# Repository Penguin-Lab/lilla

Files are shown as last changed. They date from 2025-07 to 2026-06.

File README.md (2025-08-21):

# lilla
A Lilla é uma robô quadrúpede desenvolvida para andar de forma autônoma ou para ser controlada pelo celular. Para se locomover, ela possui 4 patas de 3 graus de liberdade cada (3 motores) e uma ESP32 que comanda o conjunto! Ela é a quarta integrante robótica do nosso espaço inteligente!

# Estrutura física
A estrutura física do robô é composta por quatro patas de três eixos cada (três motores). As patas são fixadas a uma estrutura de PLA para deixar o robô firme. As peças são todas projetadas em 3D e foram impressas utilizando PLA, podendo ser encontradas na pasta Pecas_3d deste projeto.

   

## Peças 3D em STL
As peças em 3D desenvolvidas para este projeto foram baseadas no projeto do robô desenvolvido por Andres ([LINK](https://gitlab.com/anflores/pavlov_mini)). Na pasta Pecas_3d, estão listadas essas peças em STL. Para ajudar, segue abaixo uma lista de todas as peças que devem ser impressas e qual o valor da sua maior dimensão (para ajudar na escolha da impressora):
* Corpo
  * 1x [LILLA_AXILA_FRONT_LEFT.STL (81 mm)](https://github.com/Penguin-Lab/lilla/blob/main/Pecas_3d/LILLA_AXILA_FRONT_LEFT.STL)
  * 1x [LILLA_AXILA_FRONT_RIGHT.STL (81 mm)](https://github.com/Penguin-Lab/lilla/blob/main/Pecas_3d/LILLA_AXILA_FRONT_RIGHT.STL)
  * 1x [LILLA_AXILA_BACK_LEFT.STL (81 mm)](https://github.com/Penguin-Lab/lilla/blob/main/Pecas_3d/LILLA_AXILA_BACK_LEFT.STL)
  * 1x [LILLA_AXILA_BACK_RIGHT.STL (81 mm)](https://github.com/Penguin-Lab/lilla/blob/main/Pecas_3d/LILLA_AXILA_BACK_RIGHT.STL)
  * 1x [LILLA_SUPPORT_LEFT_TOP.STL (127 mm)](https://github.com/Penguin-Lab/lilla/blob/main/Pecas_3d/LILLA_SUPPORT_LEFT_TOP.STL)
  * 1x [LILLA_SUPPORT_LEFT_TOP.STL espelhado (127 mm)](https://github.com/Penguin-Lab/lilla/blob/main/Pecas_3d/LILLA_SUPPORT_LEFT_TOP.STL)
  * 2x [LILLA_SUPPORT_FACE_BACK_UP.STL (51 mm)](https://github.com/Penguin-Lab/lilla/blob/main/Pecas_3d/LILLA_SUPPORT_FACE_BACK_UP.STL)
  * 2x [LILLA_SUPPORT_FACE_BACK_DOWN.STL (63 mm)](https://github.com/Penguin-Lab/lilla/blob/main/Pecas_3d/LILLA_SUPPORT_FACE_BACK_DOWN.STL)
  * 2x [LILLA_SUPPORT_FACE_BACK_DOWN.STL (63 mm)](https://github.com/Penguin-Lab/lilla/blob/main/Pecas_3d/LILLA_SUPPORT_FACE_BACK_DOWN.STL)
  * 2x [LILLA_SUPPORT_BOTTOM.STL (99 mm)](https://github.com/Penguin-Lab/lilla/blob/main/Pecas_3d/LILLA_SUPPORT_BOTTOM.STL)
  * 4x [LILLA_SUPPORT_PCI.STL (9 mm)](https://github.com/Penguin-Lab/lilla/blob/main/Pecas_3d/LILLA_SUPPORT_PCI.STL)
* Patas
  * 2x [LILLA_TIBIA_LEFT.STL (128 mm)](https://github.com/Penguin-Lab/lilla/blob/main/Pecas_3d/LILLA_TIBIA_LEFT.STL)
  * 2x [LILLA_TIBIA_LEFT.STL espelhado (128 mm)](https://github.com/Penguin-Lab/lilla/blob/main/Pecas_3d/LILLA_TIBIA_LEFT.STL)
  * 2x [LILLA_FEMUR_LEFT_A_1.STL (134 mm)](https://github.com/Penguin-Lab/lilla/blob/main/Pecas_3d/LILLA_FEMUR_LEFT_A_1.STL)
  * 2x [LILLA_FEMUR_LEFT_A_1.STL espelhado (134 mm)](https://github.com/Penguin-Lab/lilla/blob/main/Pecas_3d/LILLA_FEMUR_LEFT_A_1.STL)
  * 4x [LILLA_FEMUR_LEFT_A_2.STL (8 mm)](https://github.com/Penguin-Lab/lilla/blob/main/Pecas_3d/LILLA_FEMUR_LEFT_A_2.STL)
  * 2x [LILLA_FEMUR_LEFT_B.STL (134 mm)](https://github.com/Penguin-Lab/lilla/blob/main/Pecas_3d/LILLA_FEMUR_LEFT_B.STL)
  * 2x [LILLA_FEMUR_LEFT_B.STL espelhado (134 mm)](https://github.com/Penguin-Lab/lilla/blob/main/Pecas_3d/LILLA_FEMUR_LEFT_B.STL)
  * 2x [LILLA_OMBRO_LEFTFRONT_BACKRIGHT.STL (66 mm)](https://github.com/Penguin-Lab/lilla/blob/main/Pecas_3d/LILLA_OMBRO_LEFTFRONT_BACKRIGHT.STL)
  * 2x [LILLA_OMBRO_LEFTFRONT_BACKRIGHT.STL espelhado (66 mm)](https://github.com/Penguin-Lab/lilla/blob/main/Pecas_3d/LILLA_OMBRO_LEFTFRONT_BACKRIGHT.STL)
  * 8x [LILLA_TIBIA_TUBO.STL (20 mm)](https://github.com/Penguin-Lab/lilla/blob/main/Pecas_3d/LILLA_TIBIA_TUBO.STL)
* Rosto e bumbum
  * 1x [LILLA_FRONT_FRAME.STL (137 mm)](https://github.com/Penguin-Lab/lilla/blob/main/Pecas_3d/LILLA_FRONT_FRAME.STL)
  * 1x [LILLA_FACE.STL (137 mm)](https://github.com/Penguin-Lab/lilla/blob/main/Pecas_3d/LILLA_FACE.STL)
  * 1x [LILLA_BUMBUM.STL (137 mm)](https://github.com/Penguin-Lab/lilla/blob/main/Pecas_3d/LILLA_BUMBUM.STL)

Obs 1: para que as patas girem sem forçar a conexão dos eixos dos motores com as peças, são utilizados dois tipos de rolamentos para cada pata: dois rolamentos [6805-2RS 25x37x7](https://pt.aliexpress.com/item/4000347743665.html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) e um rolamentos [606-2RS 6x17x6](https://www.oliveirarolamentos.com.br/micro-rolamento-rigido-de-esferas-606-2rs-c3-6x17x6mm.html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).
Obs 2: para o comando da tibia, o motor deverá ter em seu eixo uma [polia dentada GT2 de 36 dentes para eixo de servo e correia de 6mm](https://a.aliexpress.com/_mPVv40N), e uma [correia de 6mm com 300mm de comprimento](https://a.aliexpress.com/_mN8S5o1).

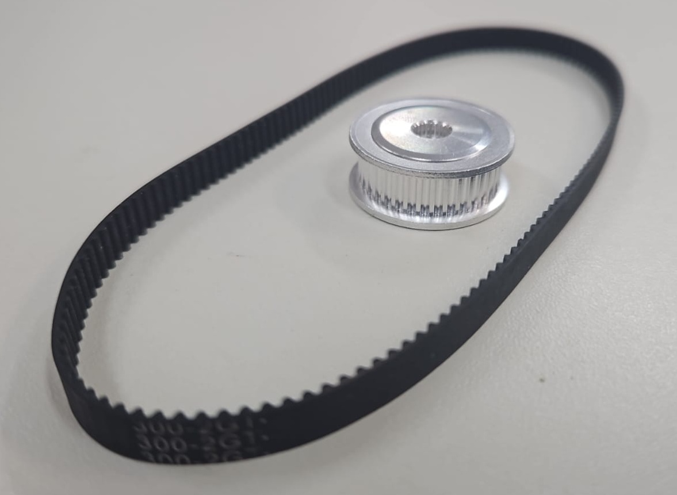
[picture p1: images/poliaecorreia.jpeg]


Obs 3: os outros motores ficam fixados nas peças por [discos metálicos pequenos padrão para eixos de servo](https://a.aliexpress.com/_mPHt3nf).

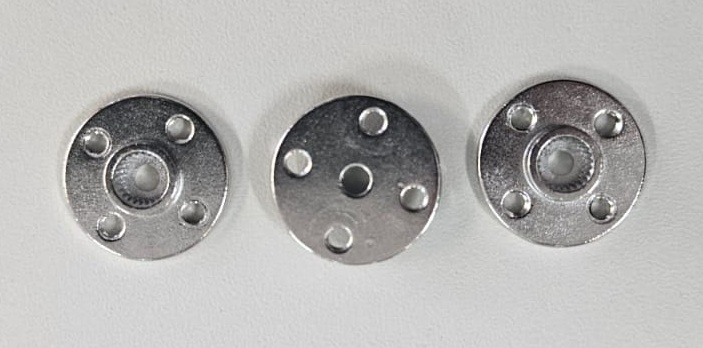
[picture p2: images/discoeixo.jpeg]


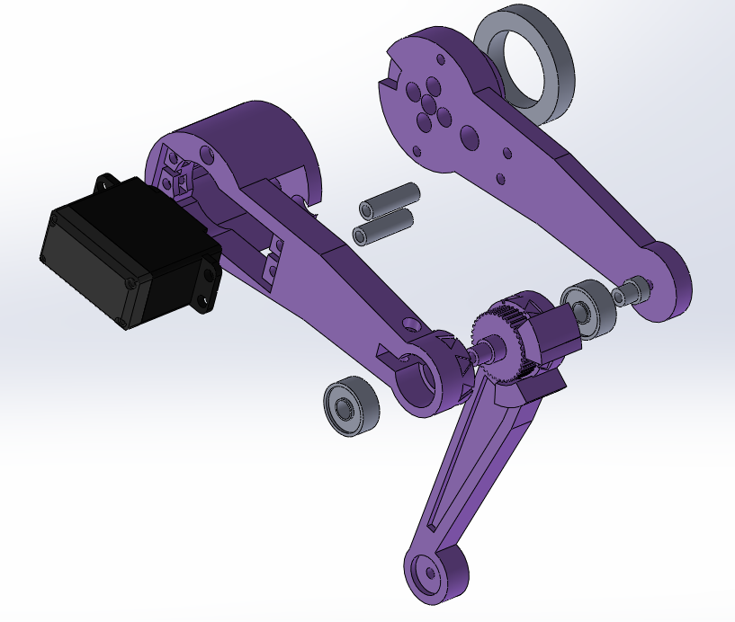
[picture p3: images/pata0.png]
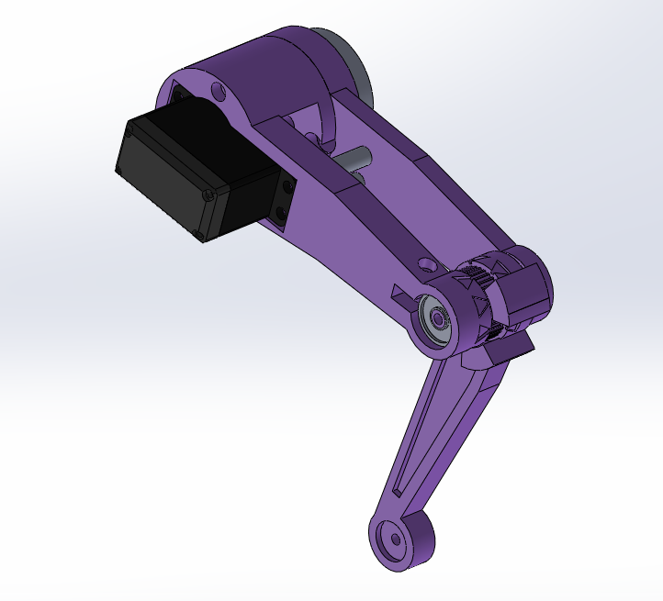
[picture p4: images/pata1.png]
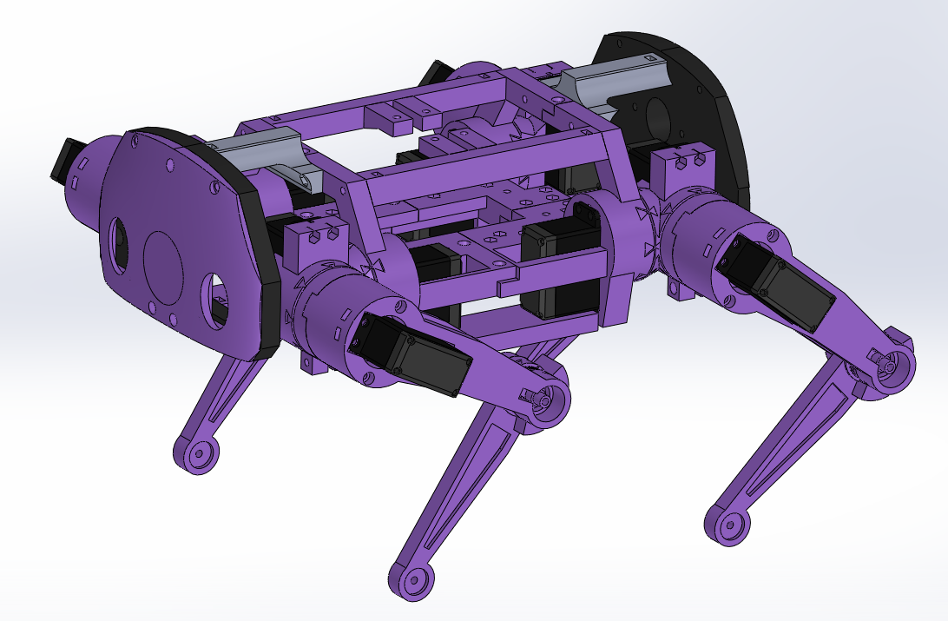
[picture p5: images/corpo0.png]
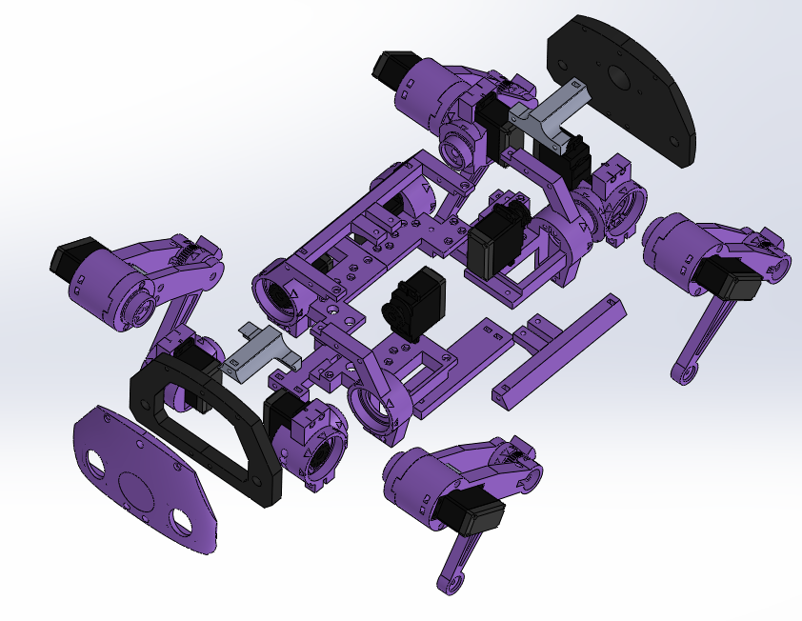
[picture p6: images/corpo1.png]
   

## Outros itens da estrutura
Alguns outros itens são necessários para finalizar a estrutura da Lilla:
* Parafusos m3 de diversos tamanhos
* 4x Tiras de EVA: colocar na ponta das peças de tibia para evitar que o robô deslize no chão

## Placa de circuito impresso
No projeto, foi desenvolvida uma placa de circuito para servir como shield para a ESP32 e conexão com a placa PCA9685 e o módulo DFPlayer Mini MP3 Player.

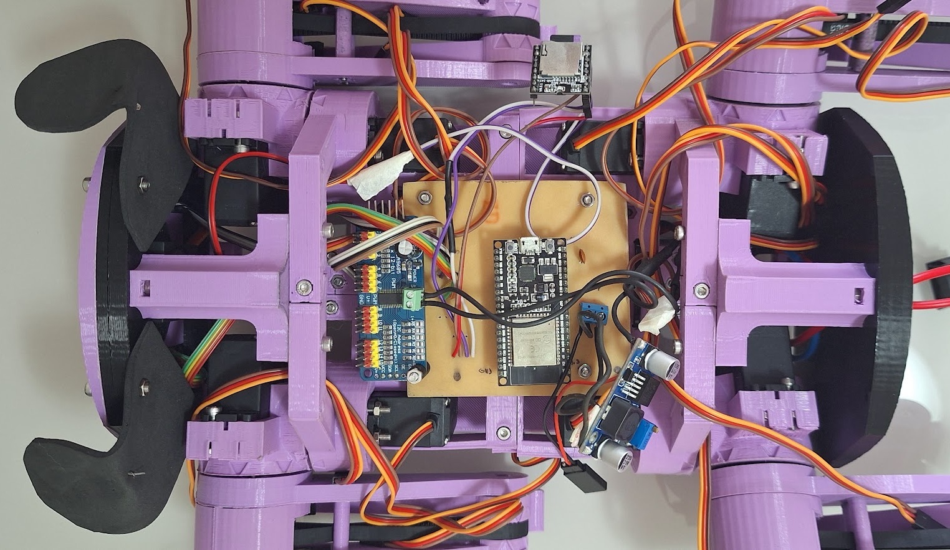
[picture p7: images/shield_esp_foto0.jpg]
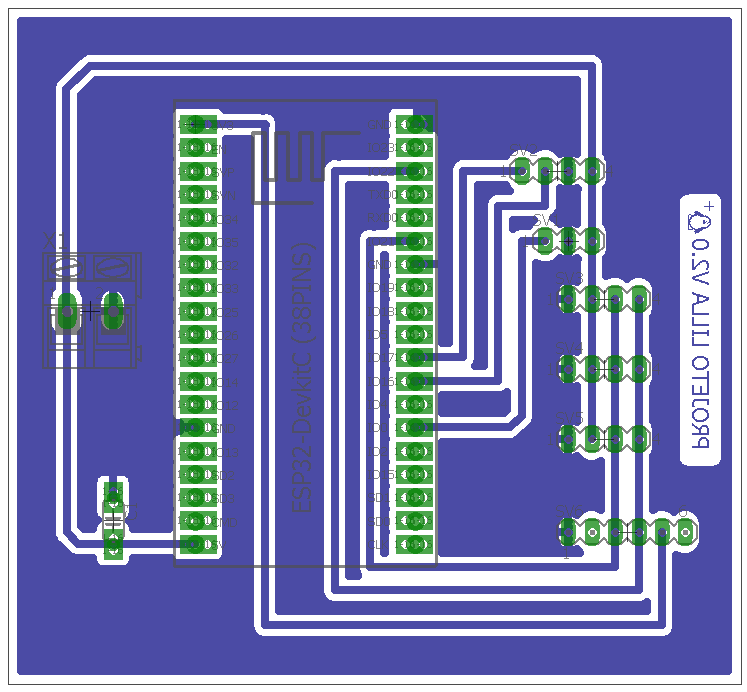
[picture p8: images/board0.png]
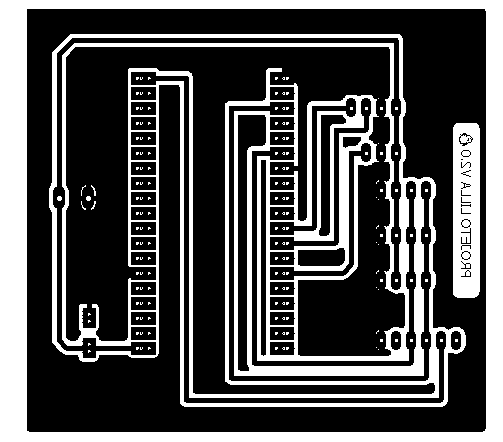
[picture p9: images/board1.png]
  

## Componentes eletrônicos
Os componentes eletrônicos embarcados no robô e equipamentos utilizados são:
* Controlador com Wi-fi e Bluetooth
  * 1x ESP32 (38 pinos)
* Motores
  * 12x Servo TowerPro MG995 Metálico
* 1x Placa PCA9685 para comando dos 12 motores
* 1x Módulo DFPlayer Mini MP3 Player com cartão micro SD contendo aúdio de latidos
* 1x Alto-falante de 3W e 4Ohm para os latidos
* Chave (switch)
* Alimentação
  * Bateria Zippy LiFe 1100mAh 2s 6,6V (ESP32)
  * Bateria TM Hobbies LiFe 2100mAh 2s 6,6v (motores)

# Software
Na pasta de códigos, há um código de programação da ESP32 (38 pinos). Ele é um exemplo em C++ do comando de movimentação da Lilla:
* Dabble: a ESP32 pode se comunicar com o aplicativo Dabble no celular e receber comandos de ação.

## Alunas participantes e desenvolvedoras da Lilla
* Ana Carolina Domingues Benisio
* Jéssica Kauany Morais Carvalho
* Maria Cecilia poton Cristovão
* Sarah Souza Mendes

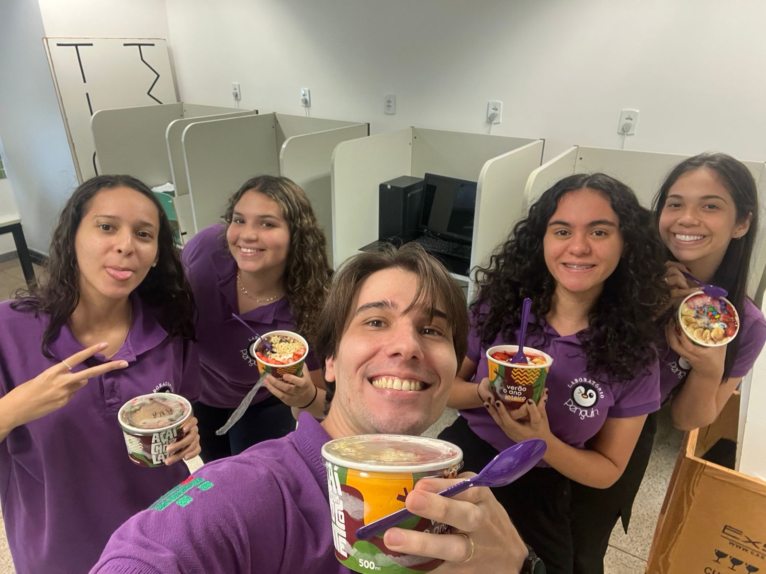
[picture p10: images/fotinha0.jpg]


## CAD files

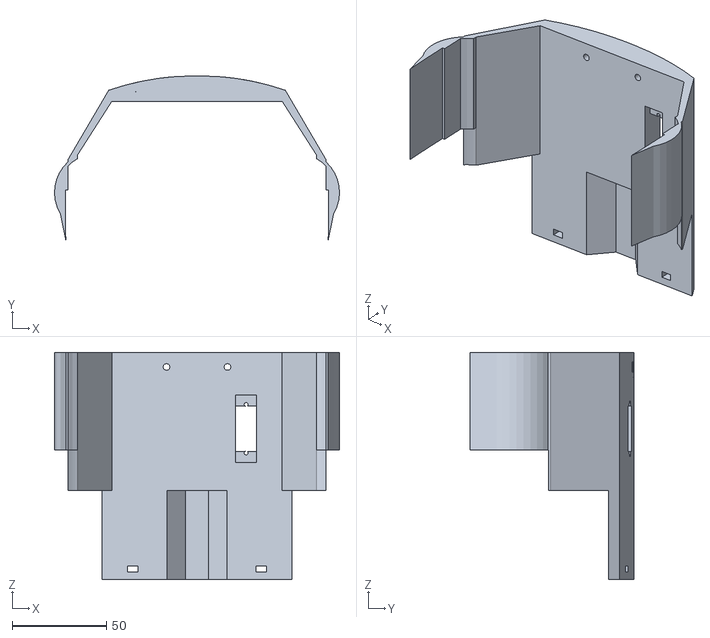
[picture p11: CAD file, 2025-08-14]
Pecas_3d/LILLA_COVER_BACK.STL
151.1 x 87.0 x 120.6

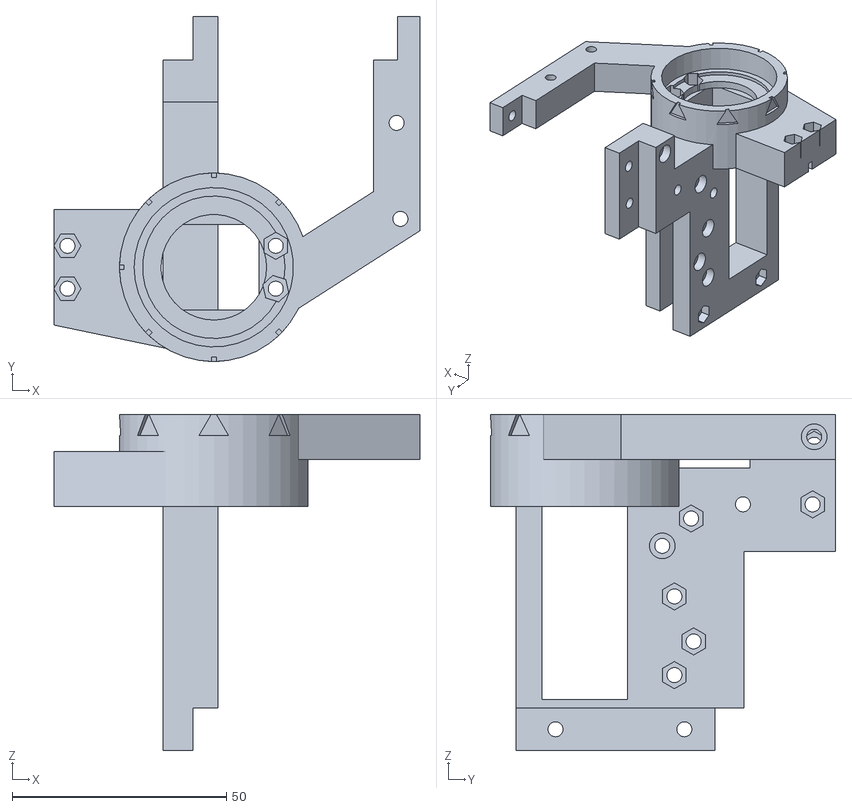
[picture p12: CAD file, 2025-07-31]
Pecas_3d/LILLA_AXILA_BACK_RIGHT.STL
85.4 x 80.5 x 78.5

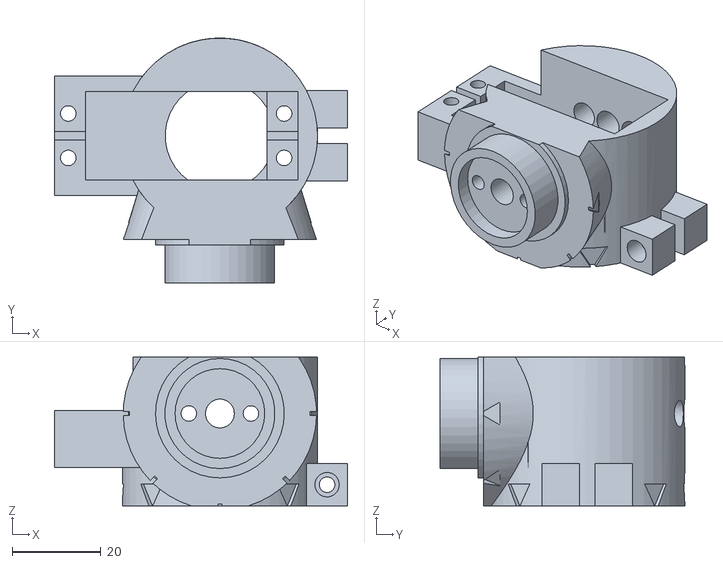
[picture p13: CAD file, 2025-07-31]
Pecas_3d/LILLA_OMBRO_LEFTFRONT_BACKRIGHT.STL
66.0 x 55.2 x 33.6

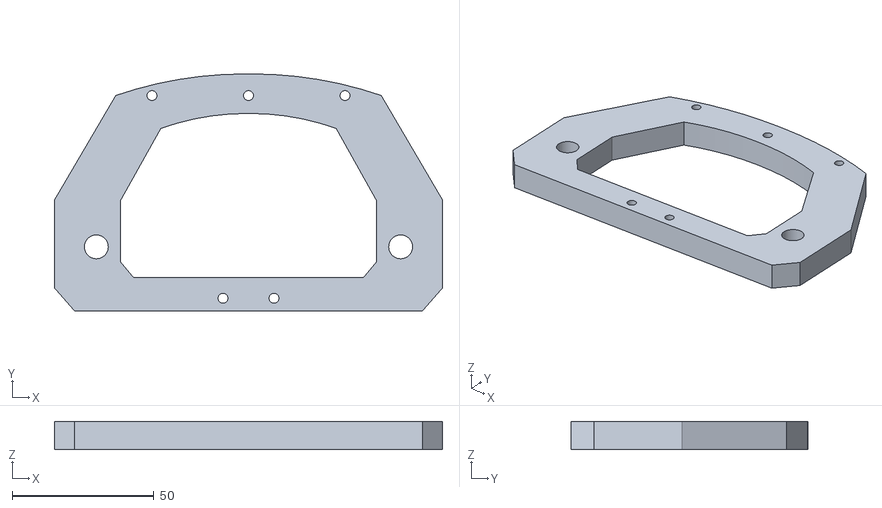
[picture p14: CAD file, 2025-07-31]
Pecas_3d/LILLA_FRONT_FRAME.STL
136.9 x 83.6 x 10.0

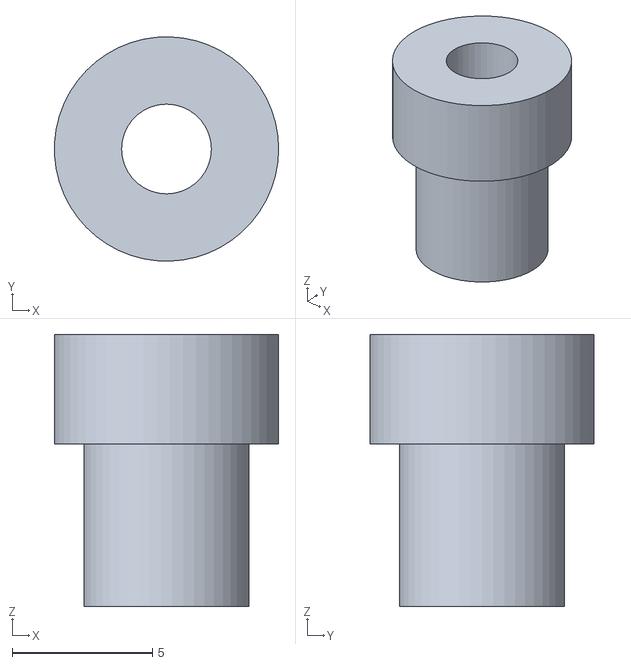
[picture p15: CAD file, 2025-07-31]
Pecas_3d/LILLA_FEMUR_LEFT_A_2.STL
8.00 x 8.00 x 9.70

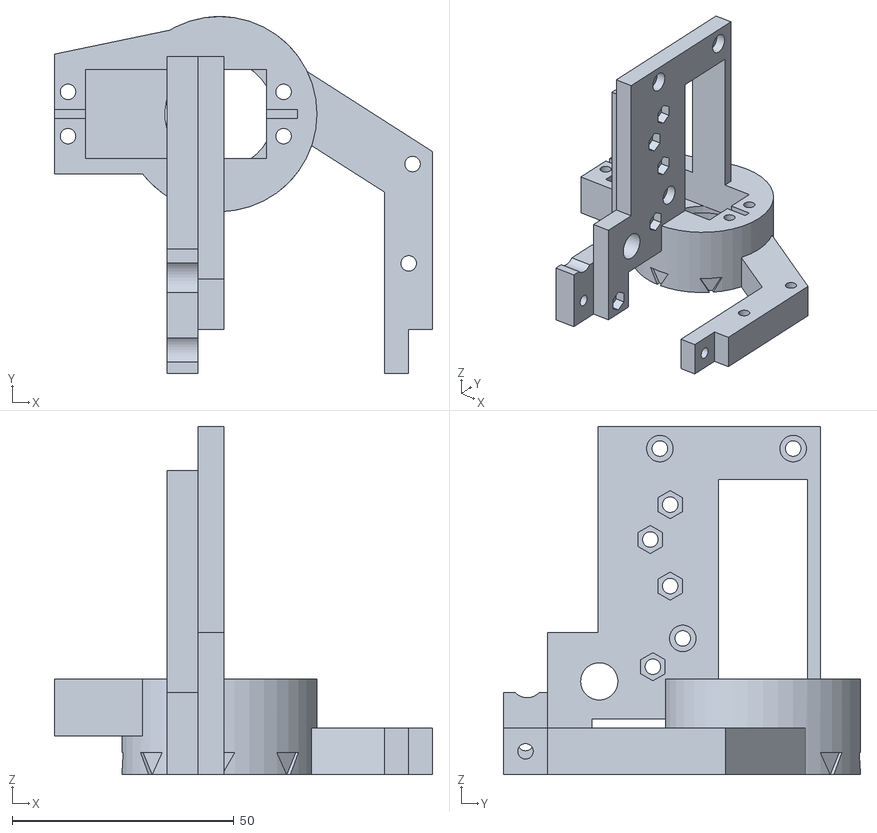
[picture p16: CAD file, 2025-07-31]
Pecas_3d/LILLA_AXILA_FRONT_LEFT.STL
85.4 x 80.5 x 78.5

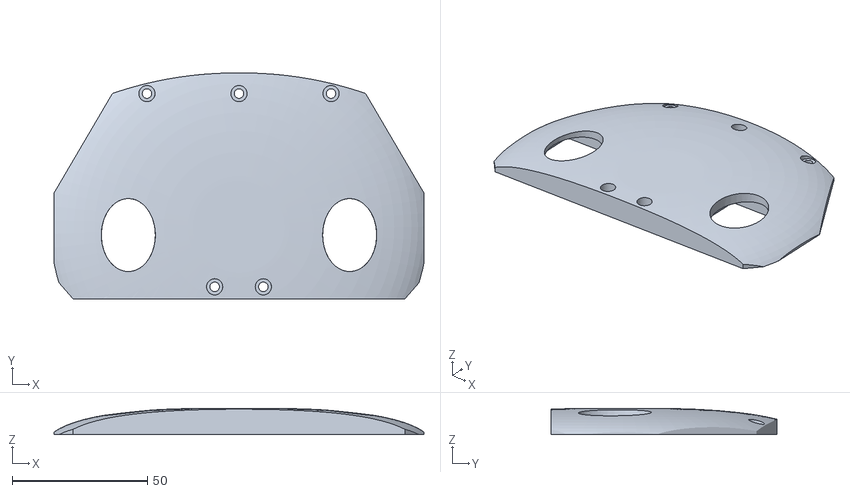
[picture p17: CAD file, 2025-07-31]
Pecas_3d/LILLA_FACE.STL
136.9 x 83.6 x 9.70

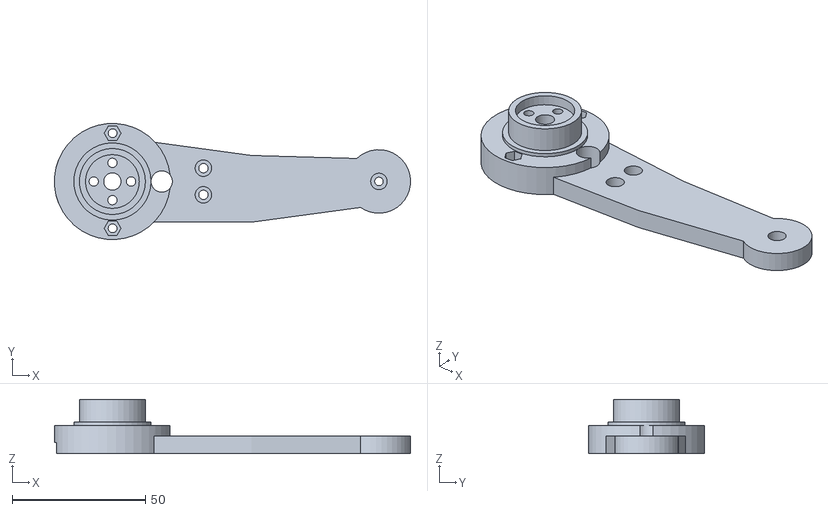
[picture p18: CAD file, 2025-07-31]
Pecas_3d/LILLA_FEMUR_LEFT_A_1.STL
133.6 x 43.5 x 20.4

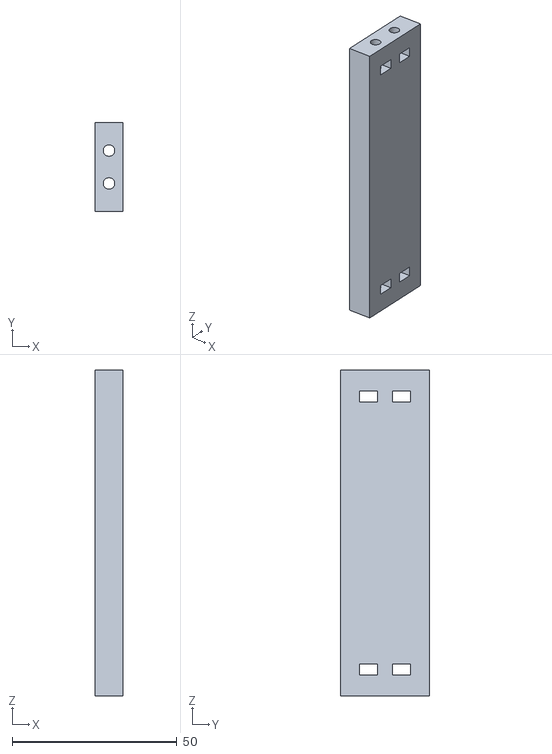
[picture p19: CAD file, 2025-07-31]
Pecas_3d/LILLA_SUPPORT_BOTTOM.STL
8.40 x 27.0 x 99.0

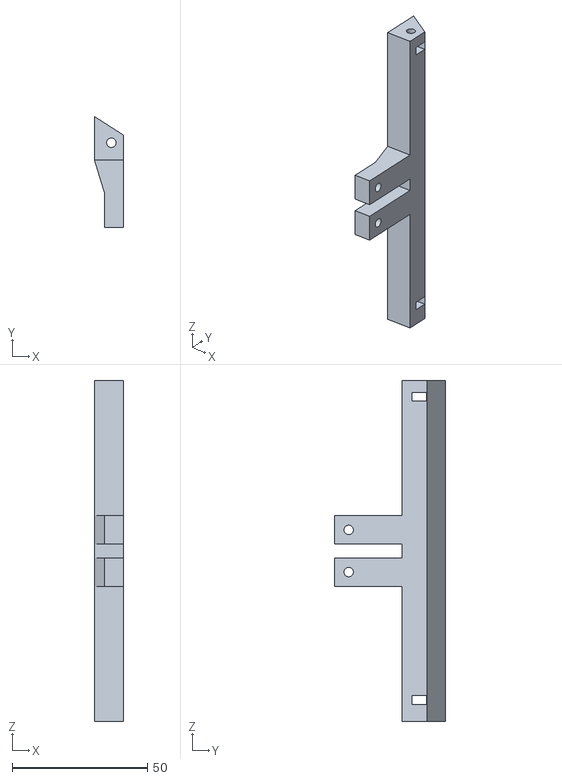
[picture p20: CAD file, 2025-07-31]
Pecas_3d/LILLA_SUPPORT_LEFT_TOP.STL
10.8 x 41.1 x 126.1

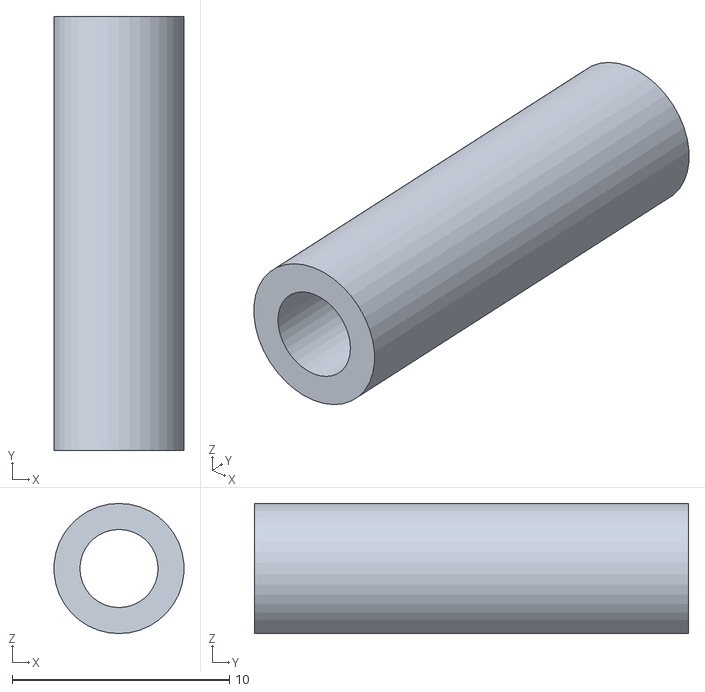
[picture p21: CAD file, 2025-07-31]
Pecas_3d/LILLA_TIBIA_TUBO.STL
5.98 x 20.0 x 6.00

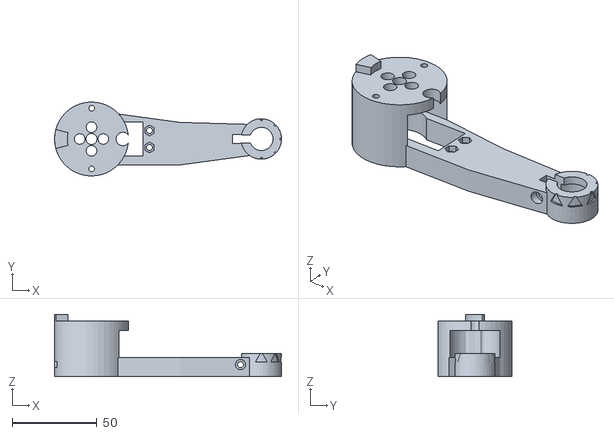
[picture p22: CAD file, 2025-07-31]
Pecas_3d/LILLA_FEMUR_LEFT_B.STL
133.7 x 43.6 x 36.7

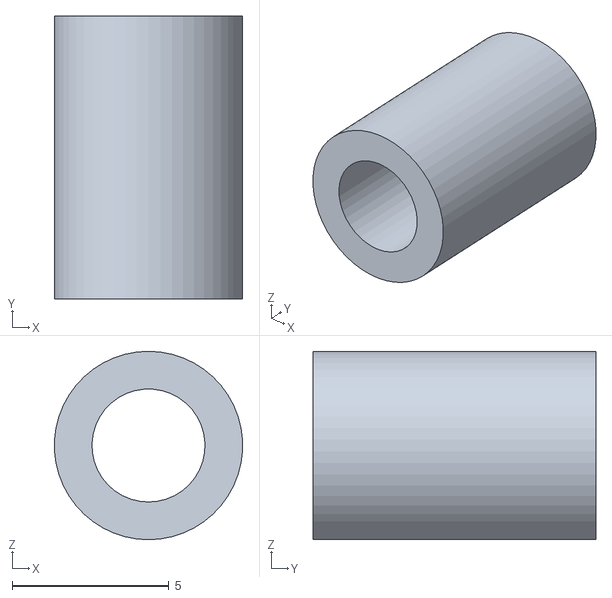
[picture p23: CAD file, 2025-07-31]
Pecas_3d/LILLA_SUPPORT_PCI.STL
5.99 x 9.00 x 6.00

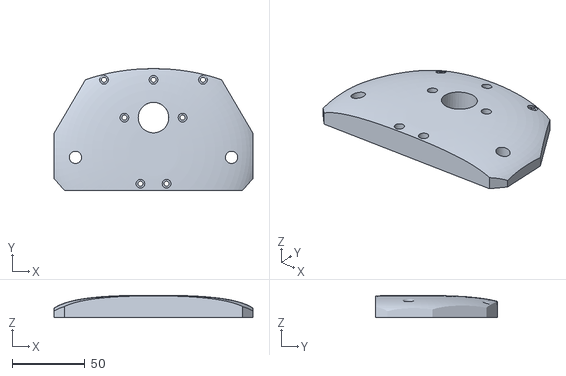
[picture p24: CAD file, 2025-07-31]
Pecas_3d/LILLA_BUMBUM.STL
136.9 x 83.6 x 15.2

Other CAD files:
Pecas_3d/LILLA_COVER_FRONT.STL
Pecas_3d/LILLA_AXILA_FRONT_RIGHT.STL
Pecas_3d/LILLA_SUPPORT_FACE_BACK_DOWN.STL
Pecas_3d/LILLA_SUPPORT_FACE_BACK_UP.STL
Pecas_3d/LILLA_AXILA_BACK_LEFT.STL
Pecas_3d/LILLA_TIBIA_LEFT.STL

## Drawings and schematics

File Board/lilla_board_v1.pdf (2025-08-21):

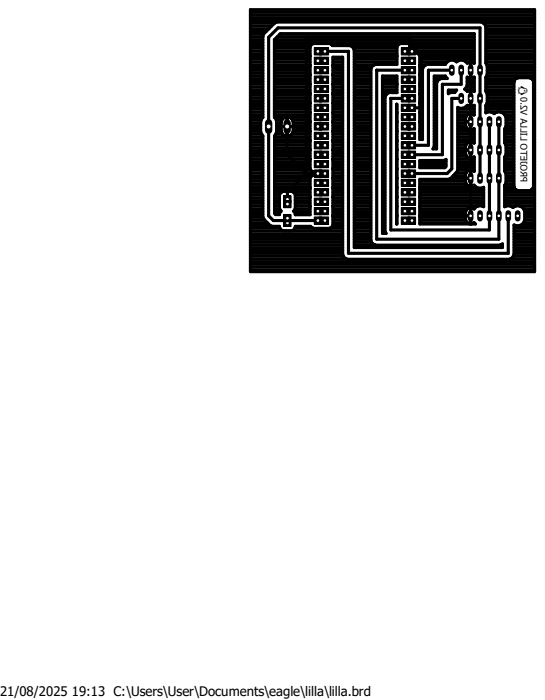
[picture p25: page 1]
21/08/2025 19:13 C:\Users\User\Documents\eagle\lilla\lilla.brd; PROJETO LILLA V2.0

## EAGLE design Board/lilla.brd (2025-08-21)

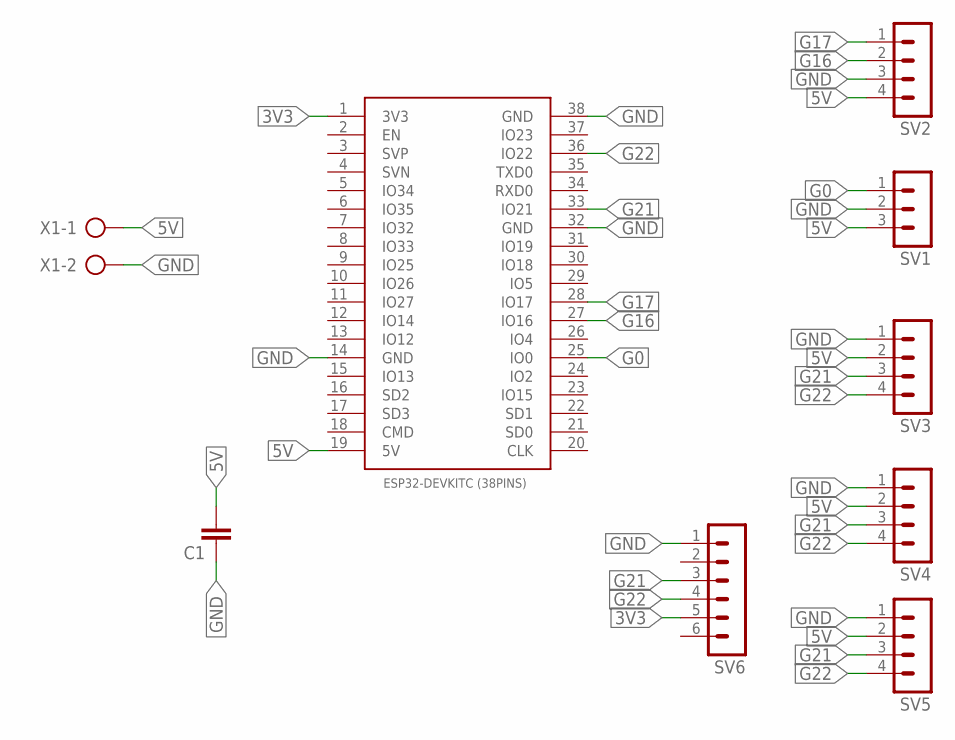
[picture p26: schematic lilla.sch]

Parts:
C1: C-EU050-024X044; C050-024X044
ESP32-DEVKITC(38PINS)2: ESP32DEVKITC_38PINS; ESP32-DEVKITC
SV1: MA03-1
SV2, SV3, SV4, SV5: MA04-1
SV6: MA06-1
X1: AK300/2

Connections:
3V3: ESP32-DEVKITC(38PINS)2.1 (3V3), SV6.5
5V: C1.2, ESP32-DEVKITC(38PINS)2.19 (5V), SV1.3, SV2.4, SV3.2, SV4.2, SV5.2, X1.1
G0: ESP32-DEVKITC(38PINS)2.25 (IO0), SV1.1
G16: ESP32-DEVKITC(38PINS)2.27 (IO16), SV2.2
G17: ESP32-DEVKITC(38PINS)2.28 (IO17), SV2.1
G21: ESP32-DEVKITC(38PINS)2.33 (IO21), SV3.3, SV4.3, SV5.3, SV6.3
G22: ESP32-DEVKITC(38PINS)2.36 (IO22), SV3.4, SV4.4, SV5.4, SV6.4
GND: C1.1, ESP32-DEVKITC(38PINS)2.14 (GND), ESP32-DEVKITC(38PINS)2.32 (GND), ESP32-DEVKITC(38PINS)2.38 (GND), SV1.2, SV2.3, SV3.1, SV4.1, SV5.1, SV6.1, X1.2

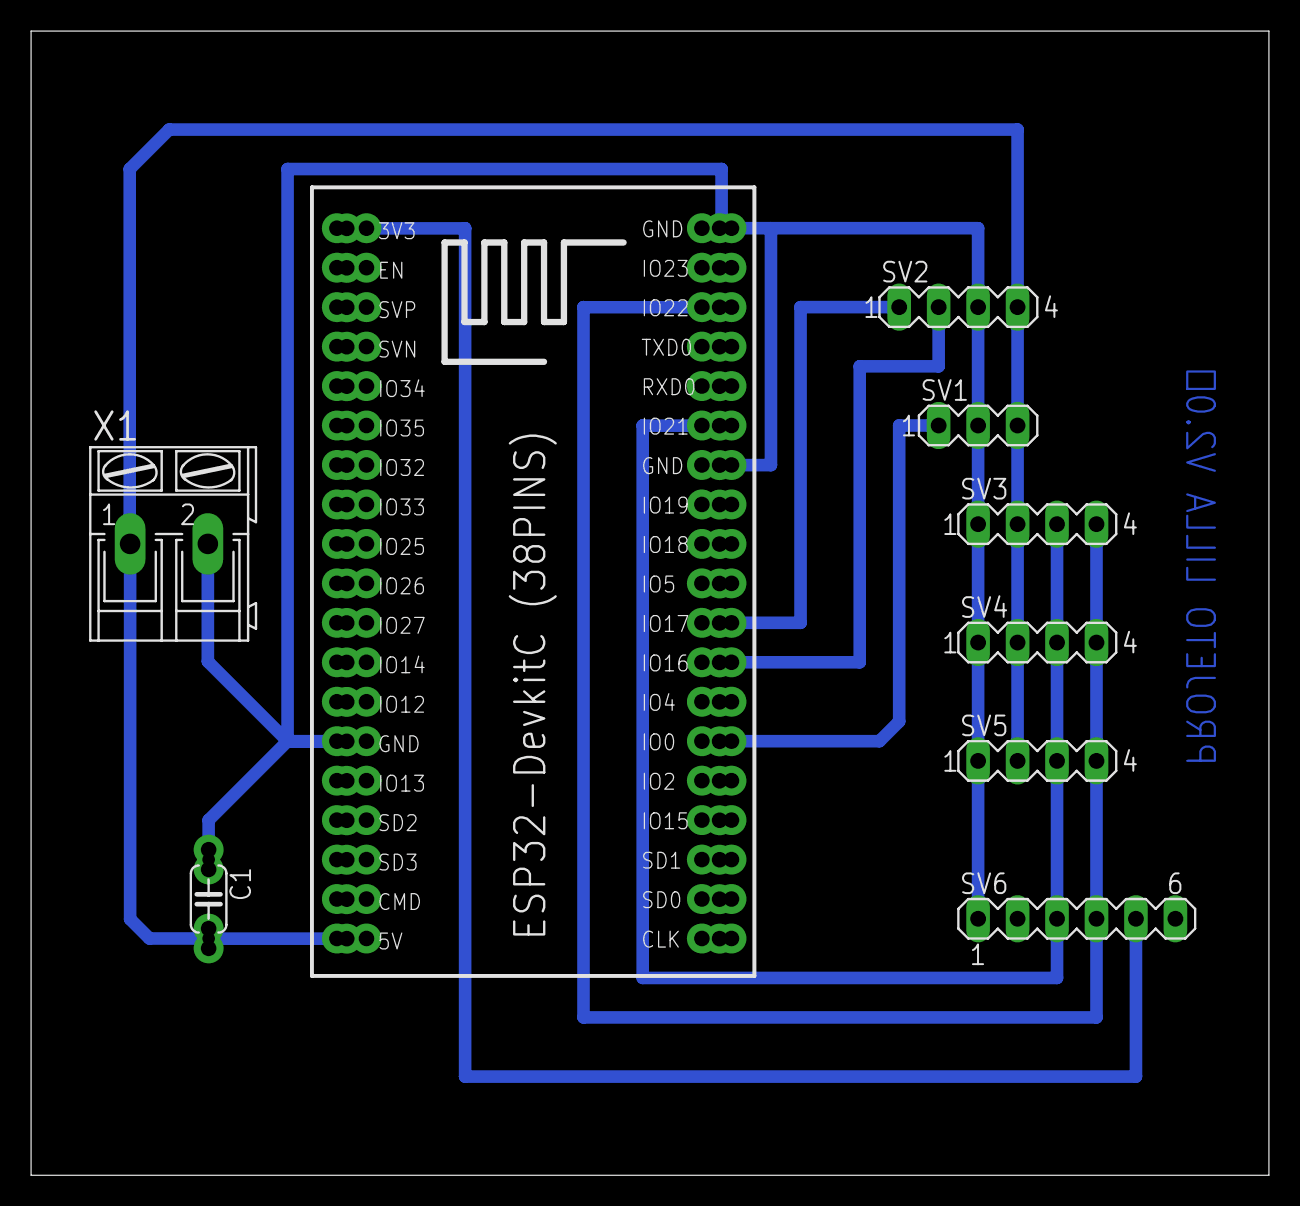
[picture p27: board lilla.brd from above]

Board: 2 copper layers, 79.7 x 73.7 mm, 9 parts (0 on the bottom side), 8 nets.

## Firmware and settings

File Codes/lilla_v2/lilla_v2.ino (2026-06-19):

#define CUSTOM_SETTINGS
#define INCLUDE_GAMEPAD_MODULE
#include <DabbleESP32.h>
#include <Wire.h>
#include <Adafruit_PWMServoDriver.h>
#include <math.h>
#include <Adafruit_GFX.h>
#include <Adafruit_SSD1306.h>
#include <HardwareSerial.h>
HardwareSerial meuSerial(2);

#define TOTAL_PONTOS 25
#define METADE_PONTOS TOTAL_PONTOS / 2
#define TOTAL_PONTOS_CIRCULAR 25
#define DEBUG_SIMULADOR false
#define TOUCH_PIN T3
#define TOUCH_VALUE 40

int OFFSET_ESQF = 0;
int OFFSET_DIRF = METADE_PONTOS;
int OFFSET_DIRT = 0;
int OFFSET_ESQT = METADE_PONTOS;

Adafruit_PWMServoDriver pwm = Adafruit_PWMServoDriver(0x40);

#define SCREEN_WIDTH 128
#define SCREEN_HEIGHT 64
#define OLED_I2C_ADDRESS1 0x3C
#define OLED_I2C_ADDRESS2 0x3D

Adafruit_SSD1306 display1(SCREEN_WIDTH, SCREEN_HEIGHT, &Wire, -1);
Adafruit_SSD1306 display2(SCREEN_WIDTH, SCREEN_HEIGHT, &Wire, -1);

// 'olhinho1', 46x46px
const unsigned char olhinho1[] PROGMEM = {
  0x00, 0x00, 0x3f, 0xf0, 0x00, 0x00, 0x00, 0x01, 0xff, 0xfe, 0x00, 0x00, 0x00, 0x07, 0xff, 0xff,
  0x80, 0x00, 0x00, 0x1f, 0xff, 0xff, 0xe0, 0x00, 0x00, 0x7f, 0xff, 0xff, 0xf8, 0x00, 0x00, 0xff,
  0xff, 0xff, 0xfc, 0x00, 0x01, 0xff, 0xff, 0xff, 0xfe, 0x00, 0x03, 0xff, 0xff, 0xff, 0xff, 0x00,
  0x07, 0xff, 0xff, 0xff, 0xff, 0x80, 0x0f, 0xff, 0xff, 0xff, 0xff, 0xc0, 0x0f, 0xff, 0xff, 0xff,
  0xff, 0xc0, 0x1f, 0xff, 0xff, 0xff, 0xff, 0xe0, 0x1f, 0xff, 0xff, 0xff, 0xff, 0xe0, 0x3f, 0xff,
  0xff, 0xff, 0xff, 0xf0, 0x3f, 0xff, 0xff, 0xff, 0xff, 0xf0, 0x7f, 0xff, 0xff, 0xff, 0xff, 0xf8,
  0x7f, 0xff, 0xff, 0xff, 0xff, 0xf8, 0x7f, 0xff, 0xff, 0xff, 0xff, 0xf8, 0xff, 0xff, 0xff, 0xff,
  0xff, 0xfc, 0xff, 0xff, 0xff, 0xff, 0xff, 0xfc, 0xff, 0xff, 0xff, 0xff, 0xff, 0xfc, 0xff, 0xff,
  0xff, 0xff, 0xff, 0xfc, 0xff, 0xff, 0xff, 0xff, 0xff, 0xfc, 0xff, 0xff, 0xff, 0xff, 0xff, 0xfc,
  0xff, 0xff, 0xff, 0xff, 0xff, 0xfc, 0xff, 0xff, 0xff, 0xff, 0xff, 0xfc, 0xff, 0xff, 0xff, 0xff,
  0xff, 0xfc, 0xff, 0xff, 0xff, 0xff, 0xff, 0xfc, 0x7f, 0xff, 0xff, 0xff, 0xff, 0xf8, 0x7f, 0xff,
  0xff, 0xff, 0xff, 0xf8, 0x7f, 0xff, 0xff, 0xff, 0xff, 0xf8, 0x3f, 0xff, 0xff, 0xff, 0xff, 0xf0,
  0x3f, 0xff, 0xff, 0xff, 0xff, 0xf0, 0x1f, 0xff, 0xff, 0xff, 0xff, 0xe0, 0x1f, 0xff, 0xff, 0xff,
  0xff, 0xe0, 0x0f, 0xff, 0xff, 0xff, 0xff, 0xc0, 0x0f, 0xff, 0xff, 0xff, 0xff, 0xc0, 0x07, 0xff,
  0xff, 0xff, 0xff, 0x80, 0x03, 0xff, 0xff, 0xff, 0xff, 0x00, 0x01, 0xff, 0xff, 0xff, 0xfe, 0x00,
  0x00, 0xff, 0xff, 0xff, 0xfc, 0x00, 0x00, 0x7f, 0xff, 0xff, 0xf8, 0x00, 0x00, 0x1f, 0xff, 0xff,
  0xe0, 0x00, 0x00, 0x07, 0xff, 0xff, 0x80, 0x00, 0x00, 0x01, 0xff, 0xfe, 0x00, 0x00, 0x00, 0x00,
  0x3f, 0xf0, 0x00, 0x00
};
// 'olhinho2', 46x46px
const unsigned char olhinho3[] PROGMEM = {
  0x00, 0x00, 0x03, 0x00, 0x00, 0x00, 0x00, 0x00, 0x07, 0x80, 0x00, 0x00, 0x00, 0x00, 0x07, 0x80,
  0x00, 0x00, 0x00, 0x00, 0x0f, 0xc0, 0x00, 0x00, 0x00, 0x00, 0x0f, 0xc0, 0x00, 0x00, 0x00, 0x00,
  0x0f, 0xc0, 0x00, 0x00, 0x00, 0x00, 0x0f, 0xc0, 0x00, 0x00, 0x00, 0x00, 0x1f, 0xe0, 0x00, 0x00,
  0x00, 0x00, 0x1f, 0xe0, 0x00, 0x00, 0x00, 0x00, 0x1f, 0xe0, 0x00, 0x00, 0x00, 0x00, 0x1f, 0xe0,
  0x00, 0x00, 0x00, 0x00, 0x1f, 0xe0, 0x00, 0x00, 0x00, 0x00, 0x1f, 0xe0, 0x00, 0x00, 0x00, 0x00,
  0x3f, 0xf0, 0x00, 0x00, 0x00, 0x00, 0x3f, 0xf0, 0x00, 0x00, 0x00, 0x00, 0x3f, 0xf0, 0x00, 0x00,
  0x00, 0x00, 0x3f, 0xf0, 0x00, 0x00, 0x00, 0x00, 0x3f, 0xf0, 0x00, 0x00, 0x00, 0x00, 0x3f, 0xf0,
  0x00, 0x00, 0x00, 0x00, 0x3f, 0xf0, 0x00, 0x00, 0x00, 0x00, 0x3f, 0xf0, 0x00, 0x00, 0x00, 0x00,
  0x3f, 0xf0, 0x00, 0x00, 0x00, 0x00, 0x3f, 0xf0, 0x00, 0x00, 0x00, 0x00, 0x3f, 0xf0, 0x00, 0x00,
  0x00, 0x00, 0x3f, 0xf0, 0x00, 0x00, 0x00, 0x00, 0x3f, 0xf0, 0x00, 0x00, 0x00, 0x00, 0x3f, 0xf0,
  0x00, 0x00, 0x00, 0x00, 0x3f, 0xf0, 0x00, 0x00, 0x00, 0x00, 0x3f, 0xf0, 0x00, 0x00, 0x00, 0x00,
  0x3f, 0xf0, 0x00, 0x00, 0x00, 0x00, 0x3f, 0xf0, 0x00, 0x00, 0x00, 0x00, 0x3f, 0xf0, 0x00, 0x00,
  0x00, 0x00, 0x3f, 0xf0, 0x00, 0x00, 0x00, 0x00, 0x1f, 0xe0, 0x00, 0x00, 0x00, 0x00, 0x1f, 0xe0,
  0x00, 0x00, 0x00, 0x00, 0x1f, 0xe0, 0x00, 0x00, 0x00, 0x00, 0x1f, 0xe0, 0x00, 0x00, 0x00, 0x00,
  0x1f, 0xe0, 0x00, 0x00, 0x00, 0x00, 0x1f, 0xe0, 0x00, 0x00, 0x00, 0x00, 0x0f, 0xc0, 0x00, 0x00,
  0x00, 0x00, 0x0f, 0xc0, 0x00, 0x00, 0x00, 0x00, 0x0f, 0xc0, 0x00, 0x00, 0x00, 0x00, 0x0f, 0xc0,
  0x00, 0x00, 0x00, 0x00, 0x07, 0x80, 0x00, 0x00, 0x00, 0x00, 0x07, 0x80, 0x00, 0x00, 0x00, 0x00,
  0x03, 0x00, 0x00, 0x00
};
// 'olhinho3', 46x46px
const unsigned char olhinho2[] PROGMEM = {
  0x00, 0x00, 0x3f, 0xe0, 0x00, 0x00, 0x00, 0x01, 0xff, 0xf0, 0x00, 0x00, 0x00, 0x07, 0xff, 0xf8,
  0x00, 0x00, 0x00, 0x1f, 0xff, 0xf8, 0x00, 0x00, 0x00, 0x7f, 0xff, 0xf8, 0x00, 0x00, 0x00, 0xff,
  0xff, 0xfc, 0x00, 0x00, 0x01, 0xff, 0xff, 0xfc, 0x00, 0x00, 0x03, 0xff, 0xff, 0xfc, 0x00, 0x00,
  0x07, 0xff, 0xff, 0xfe, 0x00, 0x00, 0x0f, 0xff, 0xff, 0xfe, 0x00, 0x00, 0x0f, 0xff, 0xff, 0xfe,
  0x00, 0x00, 0x1f, 0xff, 0xff, 0xff, 0x00, 0x00, 0x1f, 0xff, 0xff, 0xff, 0x00, 0x00, 0x3f, 0xff,
  0xff, 0xff, 0x00, 0x00, 0x3f, 0xff, 0xff, 0xff, 0x80, 0x00, 0x7f, 0xff, 0xff, 0xff, 0x80, 0x00,
  0x7f, 0xff, 0xff, 0xff, 0x80, 0x00, 0x7f, 0xff, 0xff, 0xff, 0xc0, 0x00, 0xff, 0xff, 0xff, 0xff,
  0xc0, 0x00, 0xff, 0xff, 0xff, 0xff, 0xc0, 0x00, 0xff, 0xff, 0xff, 0xff, 0xe0, 0x00, 0xff, 0xff,
  0xff, 0xff, 0xe0, 0x00, 0xff, 0xff, 0xff, 0xff, 0xe0, 0x00, 0xff, 0xff, 0xff, 0xff, 0xf0, 0x00,
  0xff, 0xff, 0xff, 0xff, 0xf0, 0x00, 0xff, 0xff, 0xff, 0xff, 0xf0, 0x00, 0xff, 0xff, 0xff, 0xff,
  0xf0, 0x00, 0xff, 0xff, 0xff, 0xff, 0xf8, 0x00, 0x7f, 0xff, 0xff, 0xff, 0xf8, 0x00, 0x7f, 0xff,
  0xff, 0xff, 0xf8, 0x00, 0x7f, 0xff, 0xff, 0xff, 0xfc, 0x00, 0x3f, 0xff, 0xff, 0xff, 0xfc, 0x00,
  0x3f, 0xff, 0xff, 0xff, 0xfc, 0x00, 0x1f, 0xff, 0xff, 0xff, 0xfe, 0x00, 0x1f, 0xff, 0xff, 0xff,
  0xfe, 0x00, 0x0f, 0xff, 0xff, 0xff, 0xfe, 0x00, 0x0f, 0xff, 0xff, 0xff, 0xff, 0x00, 0x07, 0xff,
  0xff, 0xff, 0xff, 0x00, 0x03, 0xff, 0xff, 0xff, 0xff, 0x00, 0x01, 0xff, 0xff, 0xff, 0xfe, 0x00,
  0x00, 0xff, 0xff, 0xff, 0xfc, 0x00, 0x00, 0x7f, 0xff, 0xff, 0xf8, 0x00, 0x00, 0x1f, 0xff, 0xff,
  0xe0, 0x00, 0x00, 0x07, 0xff, 0xff, 0x80, 0x00, 0x00, 0x01, 0xff, 0xfe, 0x00, 0x00, 0x00, 0x00,
  0x3f, 0xf0, 0x00, 0x00
};
// 'olhinho4', 46x46px
const unsigned char olhinho4[] PROGMEM = {
  0x00, 0x00, 0x1f, 0xf0, 0x00, 0x00, 0x00, 0x00, 0x3f, 0xfe, 0x00, 0x00, 0x00, 0x00, 0x7f, 0xff,
  0x80, 0x00, 0x00, 0x00, 0x7f, 0xff, 0xe0, 0x00, 0x00, 0x00, 0x7f, 0xff, 0xf8, 0x00, 0x00, 0x00,
  0xff, 0xff, 0xfc, 0x00, 0x00, 0x00, 0xff, 0xff, 0xfe, 0x00, 0x00, 0x00, 0xff, 0xff, 0xff, 0x00,
  0x00, 0x01, 0xff, 0xff, 0xff, 0x80, 0x00, 0x01, 0xff, 0xff, 0xff, 0xc0, 0x00, 0x01, 0xff, 0xff,
  0xff, 0xc0, 0x00, 0x03, 0xff, 0xff, 0xff, 0xe0, 0x00, 0x03, 0xff, 0xff, 0xff, 0xe0, 0x00, 0x03,
  0xff, 0xff, 0xff, 0xf0, 0x00, 0x07, 0xff, 0xff, 0xff, 0xf0, 0x00, 0x07, 0xff, 0xff, 0xff, 0xf8,
  0x00, 0x07, 0xff, 0xff, 0xff, 0xf8, 0x00, 0x0f, 0xff, 0xff, 0xff, 0xf8, 0x00, 0x0f, 0xff, 0xff,
  0xff, 0xfc, 0x00, 0x0f, 0xff, 0xff, 0xff, 0xfc, 0x00, 0x1f, 0xff, 0xff, 0xff, 0xfc, 0x00, 0x1f,
  0xff, 0xff, 0xff, 0xfc, 0x00, 0x1f, 0xff, 0xff, 0xff, 0xfc, 0x00, 0x3f, 0xff, 0xff, 0xff, 0xfc,
  0x00, 0x3f, 0xff, 0xff, 0xff, 0xfc, 0x00, 0x3f, 0xff, 0xff, 0xff, 0xfc, 0x00, 0x3f, 0xff, 0xff,
  0xff, 0xfc, 0x00, 0x7f, 0xff, 0xff, 0xff, 0xfc, 0x00, 0x7f, 0xff, 0xff, 0xff, 0xf8, 0x00, 0x7f,
  0xff, 0xff, 0xff, 0xf8, 0x00, 0xff, 0xff, 0xff, 0xff, 0xf8, 0x00, 0xff, 0xff, 0xff, 0xff, 0xf0,
  0x00, 0xff, 0xff, 0xff, 0xff, 0xf0, 0x01, 0xff, 0xff, 0xff, 0xff, 0xe0, 0x01, 0xff, 0xff, 0xff,
  0xff, 0xe0, 0x01, 0xff, 0xff, 0xff, 0xff, 0xc0, 0x03, 0xff, 0xff, 0xff, 0xff, 0xc0, 0x03, 0xff,
  0xff, 0xff, 0xff, 0x80, 0x03, 0xff, 0xff, 0xff, 0xff, 0x00, 0x01, 0xff, 0xff, 0xff, 0xfe, 0x00,
  0x00, 0xff, 0xff, 0xff, 0xfc, 0x00, 0x00, 0x7f, 0xff, 0xff, 0xf8, 0x00, 0x00, 0x1f, 0xff, 0xff,
  0xe0, 0x00, 0x00, 0x07, 0xff, 0xff, 0x80, 0x00, 0x00, 0x01, 0xff, 0xfe, 0x00, 0x00, 0x00, 0x00,
  0x3f, 0xf0, 0x00, 0x00
};
//'olhinho5'
const unsigned char olhinho5 [] PROGMEM = {
	0x00, 0x00, 0x00, 0x1f, 0x80, 0x00, 0x00, 0x00, 0x01, 0xff, 0xf0, 0x00, 0x00, 0x00, 0x01, 0xff, 
	0xf0, 0x00, 0x00, 0x00, 0x03, 0xff, 0xfc, 0x00, 0x00, 0x00, 0x1f, 0xff, 0xfe, 0x00, 0x00, 0x00, 
	0x3f, 0xff, 0xfe, 0x00, 0x00, 0x00, 0x7f, 0xff, 0xff, 0x80, 0x00, 0x00, 0x7f, 0xff, 0xff, 0x80, 
	0x00, 0x01, 0xff, 0xff, 0xff, 0x80, 0x00, 0x03, 0xff, 0xff, 0xff, 0x80, 0x00, 0x03, 0xff, 0xff, 
	0xff, 0xc0, 0x00, 0x03, 0xff, 0xff, 0xff, 0xc0, 0x00, 0x07, 0xff, 0xff, 0xff, 0xc0, 0x00, 0x1f, 
	0xff, 0xff, 0xff, 0xc0, 0x00, 0x3f, 0xff, 0xff, 0xff, 0x80, 0x00, 0x7f, 0xff, 0xff, 0xff, 0x80, 
	0x00, 0x7f, 0xff, 0xff, 0xff, 0x80, 0x00, 0x7f, 0xff, 0xff, 0xff, 0x80, 0x00, 0xff, 0xff, 0xff, 
	0xfe, 0x00, 0x03, 0xff, 0xff, 0xff, 0xfc, 0x00, 0x07, 0xff, 0xff, 0xff, 0xf8, 0x00, 0x07, 0xff, 
	0xff, 0xff, 0xf8, 0x00, 0x0f, 0xff, 0xff, 0xff, 0xf0, 0x00, 0x0f, 0xff, 0xff, 0xff, 0xf8, 0x00, 
	0x07, 0xff, 0xff, 0xff, 0xfc, 0x00, 0x07, 0xff, 0xff, 0xff, 0xfc, 0x00, 0x03, 0xff, 0xff, 0xff, 
	0xfe, 0x00, 0x00, 0xff, 0xff, 0xff, 0xfe, 0x00, 0x00, 0x7f, 0xff, 0xff, 0xff, 0x80, 0x00, 0x3f, 
	0xff, 0xff, 0xff, 0x80, 0x00, 0x3f, 0xff, 0xff, 0xff, 0x80, 0x00, 0x1f, 0xff, 0xff, 0xff, 0xc0, 
	0x00, 0x07, 0xff, 0xff, 0xff, 0xc0, 0x00, 0x07, 0xff, 0xff, 0xff, 0xc0, 0x00, 0x07, 0xff, 0xff, 
	0xff, 0xc0, 0x00, 0x03, 0xff, 0xff, 0xff, 0x80, 0x00, 0x01, 0xff, 0xff, 0xff, 0x80, 0x00, 0x00, 
	0x7f, 0xff, 0xff, 0x80, 0x00, 0x00, 0x3f, 0xff, 0xfe, 0x00, 0x00, 0x00, 0x3f, 0xff, 0xfe, 0x00, 
	0x00, 0x00, 0x1f, 0xff, 0xfe, 0x00, 0x00, 0x00, 0x0f, 0xff, 0xfc, 0x00, 0x00, 0x00, 0x03, 0xff, 
	0xf8, 0x00, 0x00, 0x00, 0x00, 0xff, 0xc0, 0x00, 0x00, 0x00, 0x00, 0xff, 0xc0, 0x00, 0x00, 0x00, 
	0x00, 0x1f, 0x80, 0x00
};
//'olinho6', 46x46px
const unsigned char olhinho6 [] PROGMEM = {
	0x00, 0x07, 0xe0, 0x00, 0x00, 0x00, 0x00, 0x0f, 0xfc, 0x00, 0x00, 0x00, 0x00, 0x0f, 0xfc, 0x00, 
	0x00, 0x00, 0x00, 0x7f, 0xff, 0x00, 0x00, 0x00, 0x00, 0xff, 0xff, 0xc0, 0x00, 0x00, 0x01, 0xff, 
	0xff, 0xe0, 0x00, 0x00, 0x01, 0xff, 0xff, 0xf0, 0x00, 0x00, 0x01, 0xff, 0xff, 0xf0, 0x00, 0x00, 
	0x07, 0xff, 0xff, 0xf8, 0x00, 0x00, 0x07, 0xff, 0xff, 0xfe, 0x00, 0x00, 0x07, 0xff, 0xff, 0xff, 
	0x00, 0x00, 0x0f, 0xff, 0xff, 0xff, 0x80, 0x00, 0x0f, 0xff, 0xff, 0xff, 0x80, 0x00, 0x0f, 0xff, 
	0xff, 0xff, 0x80, 0x00, 0x0f, 0xff, 0xff, 0xff, 0xe0, 0x00, 0x07, 0xff, 0xff, 0xff, 0xf0, 0x00, 
	0x07, 0xff, 0xff, 0xff, 0xf0, 0x00, 0x07, 0xff, 0xff, 0xff, 0xf8, 0x00, 0x01, 0xff, 0xff, 0xff, 
	0xfc, 0x00, 0x01, 0xff, 0xff, 0xff, 0xff, 0x00, 0x00, 0xff, 0xff, 0xff, 0xff, 0x80, 0x00, 0xff, 
	0xff, 0xff, 0xff, 0x80, 0x00, 0x7f, 0xff, 0xff, 0xff, 0xc0, 0x00, 0x3f, 0xff, 0xff, 0xff, 0xc0, 
	0x00, 0x7f, 0xff, 0xff, 0xff, 0x80, 0x00, 0x7f, 0xff, 0xff, 0xff, 0x80, 0x00, 0xff, 0xff, 0xff, 
	0xff, 0x00, 0x01, 0xff, 0xff, 0xff, 0xfc, 0x00, 0x07, 0xff, 0xff, 0xff, 0xf8, 0x00, 0x07, 0xff, 
	0xff, 0xff, 0xf8, 0x00, 0x07, 0xff, 0xff, 0xff, 0xf8, 0x00, 0x07, 0xff, 0xff, 0xff, 0xf0, 0x00, 
	0x0f, 0xff, 0xff, 0xff, 0xe0, 0x00, 0x0f, 0xff, 0xff, 0xff, 0x80, 0x00, 0x0f, 0xff, 0xff, 0xff, 
	0x00, 0x00, 0x0f, 0xff, 0xff, 0xff, 0x00, 0x00, 0x07, 0xff, 0xff, 0xff, 0x00, 0x00, 0x07, 0xff, 
	0xff, 0xfe, 0x00, 0x00, 0x07, 0xff, 0xff, 0xf8, 0x00, 0x00, 0x07, 0xff, 0xff, 0xf8, 0x00, 0x00, 
	0x01, 0xff, 0xff, 0xf0, 0x00, 0x00, 0x01, 0xff, 0xff, 0xe0, 0x00, 0x00, 0x00, 0xff, 0xff, 0x00, 
	0x00, 0x00, 0x00, 0x3f, 0xfe, 0x00, 0x00, 0x00, 0x00, 0x3f, 0xfe, 0x00, 0x00, 0x00, 0x00, 0x07, 
	0xe0, 0x00, 0x00, 0x00
};

struct int3 {
    int ombro, femur, tibia;

    // Soma
    int3 operator+(const int3& rhs) const {
      return { ombro + rhs.ombro, femur + rhs.femur, tibia + rhs.tibia };
    }

    // Subtracao
    int3 operator-(const int3& rhs) const {
      return { ombro - rhs.ombro, femur - rhs.femur, tibia - rhs.tibia };
    }

    // Multiplicacao por escalar
    int3 operator*(int scalar) const {
      return { ombro * scalar, femur * scalar, tibia * scalar };
    }

    // Divisao por escalar
    int3 operator/(int scalar) const {
      return { ombro / scalar, femur / scalar, tibia / scalar };
    }
};

struct float3 {
    float ombro, femur, tibia;

    // Soma
    float3 operator+(const float3& rhs) const {
      return { ombro + rhs.ombro, femur + rhs.femur, tibia + rhs.tibia };
    }

    // Subtracao
    float3 operator-(const float3& rhs) const {
      return { ombro - rhs.ombro, femur - rhs.femur, tibia - rhs.tibia };
    }

    // Multiplicacao por escalar
    float3 operator*(float scalar) const {
      return { ombro * scalar, femur * scalar, tibia * scalar };
    }

    // Divisao por escalar
    float3 operator/(float scalar) const {
      return { ombro / scalar, femur / scalar, tibia / scalar };
    }
};

int3 radToDegree(float3 angles_rad){
    return {int(angles_rad.ombro * 180.0 / M_PI),int(angles_rad.femur * 180.0 / M_PI),int(angles_rad.tibia * 180.0 / M_PI)};
}

float3 degreeToRad(int3 angles){
    return {float(angles.ombro) * M_PI / 180.0,float(angles.femur) * M_PI / 180.0,float(angles.tibia) * M_PI / 180.0};
}

struct floatxyz {
    float x, y, z;

    // Soma
    floatxyz operator+(const floatxyz& rhs) const {
      return { x + rhs.x, y + rhs.y, z + rhs.z };
    }

    // Subtracao
    floatxyz operator-(const floatxyz& rhs) const {
      return { x - rhs.x, y - rhs.y, z - rhs.z };
    }

    // Multiplicacao por escalar
    floatxyz operator*(float scalar) const {
      return { x * scalar, y * scalar, z * scalar };
    }

    // Divisao por escalar
    floatxyz operator/(float scalar) const {
      return { x / scalar, y / scalar, z / scalar };
    }

    floatxyz operator*(const floatxyz& rhs) const {
      return { x * rhs.x, y * rhs.y, z * rhs.z };
    }
};

float joystickToRad(int joystickAngle){
  float angle_rad = (float(joystickAngle)-90.0)*M_PI/180.0;
  while (angle_rad > M_PI) angle_rad -= 2*M_PI;
  while (angle_rad < -M_PI) angle_rad += 2*M_PI;
  return angle_rad;
}

int joystickToInt(int joystickAngle, int deltaAngle){
  int angle = joystickAngle-90;
  while (angle > 180) angle -= 360;
  while (angle < -180) angle += 360;
  // Verifica faixas e "trava" no valor mais proximo
  if (abs(angle - 180) <= deltaAngle || abs(angle + 180) <= deltaAngle){
    return 180;
  }
  else if (abs(angle - 90) <= deltaAngle){
    return 90;
  }
  else if (abs(angle + 90) <= deltaAngle){
    return -90;
  }
  else if (abs(angle) <= deltaAngle){
    return 0;
  }
  return angle;
}
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
void loop(){
}

int estado_comando = 0;
int estado_piscando = 0;
int estado_coracao = 0;
int dt_coracao = 4000;
int dt_piscada = 100;
int dt_aberto = 8000;
int dt_brava = 30000;  //60000 = 1min

void TaskDisplays(void *pvParameters) {
  for (;;) {
    if (estado_piscando == 0) {
      if ((millis() - tempo_piscada) > dt_aberto) {
        display1.clearDisplay();
        display1.drawBitmap(41, 9, olhinho3, 46, 46, WHITE);
        display1.display();

        display2.clearDisplay();
        display2.drawBitmap(41, 9, olhinho3, 46, 46, WHITE);
        display2.display();
        estado_piscando = 1;
        tempo_piscada = millis();
        vTaskDelay(pdMS_TO_TICKS(20));
      } else {
        if (estado_comando == 0) {
          if ((millis() - tempo_comando) > dt_brava) {
            estado_comando = 1;
            tempo_olho_mau = millis();
          } else {
            display1.clearDisplay();
            display1.drawBitmap(41, 9, olhinho1, 46, 46, WHITE);
            display1.display();

            display2.clearDisplay();
            display2.drawBitmap(41, 9, olhinho1, 46, 46, WHITE);
            display2.display();
            vTaskDelay(pdMS_TO_TICKS(20));  // Tempo para o olho ficar aberto
          }
        } else if (estado_comando == 1) {
          if ((millis() - tempo_comando) < dt_brava) {
            estado_comando = 0;
          } else if ((millis() - tempo_olho_mau) > 2000) {
            estado_comando = 2;
            tempo_olho_mau = millis();
          } else {
            display1.clearDisplay();
            display1.drawBitmap(41, 9, olhinho2, 46, 46, WHITE);
            display1.display();

            display2.clearDisplay();
            display2.drawBitmap(41, 9, olhinho4, 46, 46, WHITE);
            display2.display();
            vTaskDelay(pdMS_TO_TICKS(20));  // Tempo para o olho ficar aberto
          }
        } else if (estado_comando == 2) {
          if ((millis() - tempo_comando) < dt_brava) {
            estado_comando = 0;
          } else if ((millis() - tempo_olho_mau) > 2000) {
            estado_comando = 1;
            tempo_olho_mau = millis();
          } else {
            display1.clearDisplay();
            display1.drawBitmap(41, 18, olhinho2, 46, 46, WHITE);
            display1.display();

            display2.clearDisplay();
            display2.drawBitmap(41, 0, olhinho4, 46, 46, WHITE);
            display2.display();
            vTaskDelay(pdMS_TO_TICKS(20));  // Tempo para o olho ficar aberto
          }
        }
        else{
          // Olho coracao
          if ((millis() - tempo_coracao) > dt_coracao) {
            estado_comando = 0;
            tempo_comando = millis();
          } else {
            display1.clearDisplay();
            display1.drawBitmap(41, 0, olhinho5, 46, 46, WHITE);
            display1.display();

            display2.clearDisplay();
            display2.drawBitmap(41, 0, olhinho6, 46, 46, WHITE);
            display2.display();
            vTaskDelay(pdMS_TO_TICKS(20));  // Tempo para o olho ficar aberto
          }
        }
      }
    } else {
      if ((millis() - tempo_piscada) > dt_piscada) {
        estado_piscando = 0;
        tempo_piscada = millis();
      }
    }
  }
}

int estado = 11;
int angle_joystick = 90;
int mode = 0; // 0 - Omnidirecional, 1 - Rotacional

void TaskQuadruped(void *pvParameters) {
  int k = 0;
  int totalPontos = TOTAL_PONTOS;
  for (;;) {
    if(estado == 1){ // "Dar a patinha": move patinha para a posição X = [x_ini+10;y_ini;z_ini+10]
        totalPontos = 50;
        int3 angles = {-10,-10,0};
        // lilla.darPatinha(k,totalPontos);
        lilla.darPatinhaAlto(k,angles,totalPontos);
        #if DEBUG_SIMULADOR
			    lilla.enviarAngulos(k);
		    #endif
        if (k < (totalPontos/2)){
          k++;
        }
        vTaskDelay(pdMS_TO_TICKS(2));
    }
    else if(estado == 2){ // Rebola
        // int3 angles = {20,0,0};
        int3 angles = lilla.circularRollPitchYaw(k, 10);
        lilla.cinematicaInversaCorpo(angles);
        #if DEBUG_SIMULADOR
          lilla.enviarAngulos(k);
        #endif				 
        if (k == TOTAL_PONTOS_CIRCULAR - 1){
          k = 0;
        }
        else{
          k++;
        }
        vTaskDelay(pdMS_TO_TICKS(20));
    }
    else if(estado == 3){ // Andar omnidirecional ou rotacional
        float angle = joystickToInt(angle_joystick,20);
        if (mode == 0){
          float angle_rad = angle*M_PI/180.0;
          k = lilla.andar(k,angle_rad);
        }
        else{
          k = lilla.andarCircular(k,angle);
        }
        #if DEBUG_SIMULADOR
          lilla.enviarAngulos(k);
        #endif				 
        vTaskDelay(pdMS_TO_TICKS(20));
    }
    else if(estado == 9){ // Arma
        lilla.ligarQuadruped();
        estado = 0;
        vTaskDelay(pdMS_TO_TICKS(500));
    }
    else if(estado == 10){ // Desarma
        lilla.desligarQuadruped();
        estado = 11;
        vTaskDelay(pdMS_TO_TICKS(1));
    }
    else if(estado == 0){
      k = 0;
      lilla.parar();
      #if DEBUG_SIMULADOR
        lilla.enviarAngulos(k);
      #endif	   
      vTaskDelay(pdMS_TO_TICKS(15));
    }
    else{
      vTaskDelay(pdMS_TO_TICKS(10));
    }
  }
}

void TaskComunicacao(void *pvParameters) {
  for (;;) {
    Dabble.processInput();
    if (estado != 11){
      if (GamePad.isRightPressed()||GamePad.isLeftPressed()){       // Modo rotacional
        mode = 1;
        tempo_comando = millis();
      }
      if (GamePad.isUpPressed()||GamePad.isDownPressed()){       // Modo omnidirecional
        mode = 0;
        tempo_comando = millis();
      }
      if (GamePad.isSquarePressed()) {
        playTrack(1);
      }
      if (GamePad.isCirclePressed()){       // "Dar a patinha"
        estado = 1;
        tempo_comando = millis();
      }
      else if (GamePad.isTrianglePressed()) {
        playTrack(1);
        estado_comando = 3;
        tempo_coracao = millis();
      }
      // if(GamePad.isTrianglePressed()){ // Rebola
      //   estado = 2;
      //   tempo_comando = millis();
      // }
      else if(GamePad.getRadius() > 2){     // Andar omnidirecional
        angle_joystick = GamePad.getAngle();
        estado = 3;
        tempo_comando = millis();
      }
      else if(GamePad.isSelectPressed()){   // Desarma
        estado = 10;
        tempo_comando = millis();
      }
      else{
        estado = 0;
      }
    }
    else{
      if(GamePad.isStartPressed()){         // Arma
        estado = 9;
        tempo_comando = millis();
      }
    }
    vTaskDelay(pdMS_TO_TICKS(20));   
  }
}
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
